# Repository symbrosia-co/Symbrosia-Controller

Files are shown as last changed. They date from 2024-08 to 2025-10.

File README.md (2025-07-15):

# The Symbrosia Controller
As originally designed, the Symbrosia Controller is a low cost, robust, controller designed for aquaculture.  Initially developed to support on-shore seaweed farming operations in Kailua Kona, Hawai'i, the Symbrosia Controller features a customized, low-cost sensor suite and integrated control functions tailored to meet the unique demands of these environments. 

In addition to commercial use, we envision the Symbrosia Controller as a powerful educational tool. By promoting literacy in electronics, programming, and agricultural management, we hope to empower individuals and communities to innovate and thrive in the agricultural sector. Our goal is to create a community where knowledge and technology are shared to drive sustainable agricultural practices and food security worldwide.

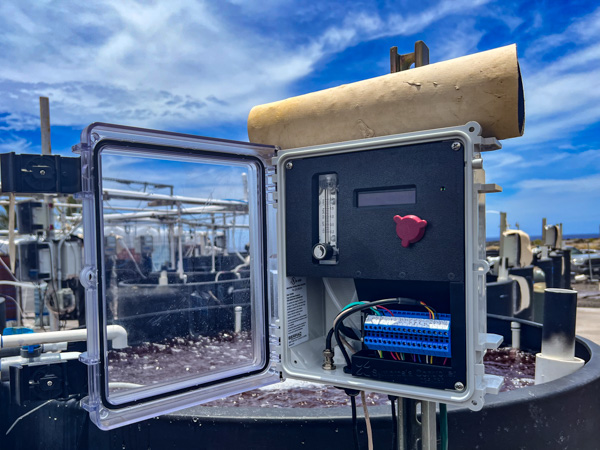
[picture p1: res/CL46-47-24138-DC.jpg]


## Background
The Symbrosia controller was developed for in-house use as a lower-cost alternative to the PLC-based and commercial off-the-shelf systems we use for algae tank and bioreactor control.  In addition to controlling the tanks there were a few other needs, places where a little remote control and monitoring is invaluable.  With the availability of WiFi processors like the ESP32 automating these functions was a practical option.

Thus the Symbrosia Controller was born…  An ESP32 wedded to a circuit board that contains the most commonly needed interfaces. A water quality sensor amplifier, some temperature inputs, a couple analog inputs, along with some relays and transistor outputs for controlling external devices like valves and pumps. 

While there are commercial solutions available, we have had mixed experience with them... The available commercial controllers are expensive and tend to provide “closed garden” systems where it becomes difficult to retrieve data outside of dedicated application software.  There is also limited or no support for integrating this equipment into a wider system.  While a number of small-scale, open source solutions do exist, none of the devices we have reviewed are fully developed into robust, industrial solutions.  As a result of our experience the Symbrosia controller offers a number of key advantages…

+ Designed from the ground up as a network appliance with full WiFi access.
+ A standard industrial ModbusTCP interface, a well established interface supported by a vast array of software and solutions available in the market.
+ A simple and effective user interface allowing access to key settings.
+ A well thought out and flexible control arrangement allowing automated control of pH, temperature, or other parameters.
+ A range of inputs that address the usual aquaculture needs...
  + One fully isolated water quality amplifier (for pH, ORP, etc.)
  + Two Pt100 temperature inputs
  + Two general purpose analog inputs that can be used with 0-5V, 0-10V, or 4-20mA signals, these can also be used as simple digital inputs.
  + Two relay outputs
  + Two open collector digital outputs
+ Good calibration solutions in place for the analog inputs
+ Semi-automated pH calibration built into the software for use with 7ph, and 4pH or 10pH reference solutions.
+ A complete solution ready for deployment in real applications.  Use it as designed and published, or change the hardware or code to suit your own needs.

Communication is via 2.4GHz WiFi, thus no cabling beyond power, or perhaps your sensors is required, a very real concern when salt water is involved and locations are scattered across a large facility. 2.4GHz offers much increased range for applications that do not require the bandwidth of higher frequencies.

For remote monitoring a ModbusTCP interface is implemented.  This allows easy integration with custom software or standard industrial SCADA systems.  While most programming languages like Python have ModbusTCP libraries available to allow connections with a few lines of code.

There are many options for designing and building a device like this.  The philosophy used in the design was carefully considered...

+ The controller is designed to be constructed and maintained by anyone with modest electronics knowledge and skills. Unless changing features is desired, no programming is required to set up and use the controller.
+ Complex solutions or specialized parts were avoided.  Rather parts that are commonly available, inexpensive, and likely to remain available for some time to come were chosen for the design.
+ An open source programming platform is used so that development tools are available at no cost, specifically the Arduino platform.
+ An open source schematic capture PCB CAD package was used, specifically KiCad. The CAD files may be used or edited at no cost beyond learning to use the software.

An example of the commonly available part philosophy can be found in the display.  There was great temptation to use a newer OLED color graphical display that would be both fun and attractive.  Rather a mundane 16x2 LCD character display was chosen.  The LDC display is very standard, inexpensive, robust in outdoor settings, available from multiple vendors, and is likely to remain available for a decade or two.  Still, a version based on an OLED display may exist someday just for the fun of it.

Another good example of this is in using a development module for the ESP32 rather than laying out the ESP32 and support electronics directly onto the main PCB.  While much of the design is surface mount, larger packages were used, this allows the entire PCB to be assembled by hand with no more specialized equipment than a decent soldering iron.

Likewise using the Arduino programming platform provides an approachable simplicity that is easily learned.  A huge array of support exists on the web with a robust development community.  Libraries to support Arduino are available from many sources that allow the use of a wide array of sensors, chips, or ready to use modules.

With the controller proving its usefulness across our algae production facility a further decision was made…  To release the controller to the community as an open source device.  Symbrosia is publishing the complete plans…  Schematic, BOM, PCB, 3D models, code, and user manual.

There is nothing exotic or particularly special here.  The Symbrosia Controller is the result of taking a number of parts and solutions that are available in the community and weaving them into a well thought out and robust solution.  The controller has been a good solution for us, maybe you can use it as well.

The Symbrosia Team

## Hardware
The Symbrosia Controler is a single circuit board that measures 120 x 92mm (4.71" x 3.62").  The board mounts an LCD display, a rotaty encoder for user input, and a pair of 8 circuit headers that permit easy connection of power and field wiring.  

The PCB assembly is designed to be mounted in either a simple case for DIN rail mounting, or for direct mounting in a control panel where the display and control knob are easily accessible.  Examples of both of these mountings can be found in the documention here including 3D models for the case.

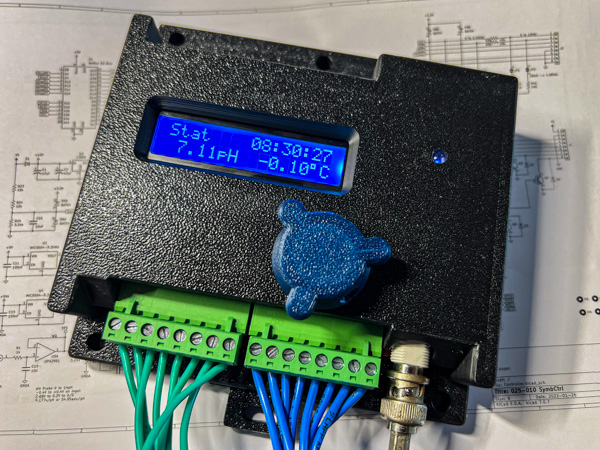
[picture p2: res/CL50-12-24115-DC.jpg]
A SymbCtrl in the DIN mount case


## Software
There are several software elements to the controller, all can be found in this repository.  While you may simply download everything here, an easier solution would be to install a copy of [GitHub desktop](https://desktop.github.com/download/).  Synchronizing with Github would allow you to keep an always up-to-date version available for use.

### Firmware
Firmware for the Symbrosia Controller was wriiten in the Arduino Framework for ESP-32.  The Arduino ecosystem is open source, free, and is amazing well supported by an enormous user community.  If you do not know how to use an Arduino device it is a good skill to learn, an incredibly useful tool to have in your skillset.

Compiling and downloading firmware to the controller is most easily accomplished by downloading the free [Arduino IDE](https://www.arduino.cc/en/software) and configuring it for use with the ESP32.  Additionally a few libraries will need to be loaded, this can be done with the library tool in the IDE.

### SyView
Setup and configuration is done through access to the Modbus regiaters.  Doing this by hand would be tedious.  To simplify this task SyView, a Python GUI is provided that gives easy access to all of the setup registers in an organized graphical app.  SyView also allows downloading complete configurations so they may be stored or loaded to multiple units with a single click. 

### MbMon
MbMon is a ModbusTCP data logger.  This script is often used to do simple datalogging for testing and short experiments.  An XML configuration file is used to designate a few Modbus devices on a local network.  The specified registers are monitored and if needed logged to a CSV file that can be used for data analysis.

MbMon will work with any ModbusTCP device including SymbCtrl, it can also serve as example code for writing your own logging application.

## Examples
Currently three sample systems are documented here, use these setups as is, or modify them to your own needs...

* [Tank or PBR controller](/samples/TankController/)
* [CO<sub>2</sub> Tapping Point Monitor](/samples/CO2Monitor/)
* [Weather Station](/samples/weather/)
  
Each of these designs are provided with schematics, 3D models, and setup files for the Symbrosia Controller.



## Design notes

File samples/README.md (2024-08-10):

# Samples
Several sample uses and configurations of the Symbrosia Controller are presented here..
[Tank or PBR controller with CO<sub>2</sub>](/TankController)
[CO<sub>2</sub> Tapping Point Monitor](/CO2Monitor)
[Weather Station](/weather)

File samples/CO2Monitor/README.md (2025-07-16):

# CO<sub>2</sub> Monitor

This example uses a simple pressure monitor to provide an alarm before a CO<sub>2</sub> cylinder is exhausted.

There is a complication in using a simple pressure sensor to monitor a CO<sub>2</sub> cylinder.  As CO<sub>2</sub> is stored as a liquid under pressure in the cylinder, the pressure in the tank is not determined by the amount of gas remaining, but rather by the boiling point of CO<sub>2</sub>.  Thus the amount of remaining gas cannot be measured by monitoring the pressure as it could be with air as done in scuba tanks.

The working pressure of the tank will remain at 50 to 70 Bar (700-1000 PSI), depending on ambient temperture, until the last liquid boils off.  Only once the liquid is gone will the pressure begin to drop as the last gas from the tank is used.  Setting an alarm threshhold of around 35 Bar (500 PSI) will allow a bit of warning before the available supply of gas is totally expended.

If proper determination of the amount of remaining CO<sub>2</sub> is desired the most practical method is to place the cylinder on a scale to directly measure the weight of the remaining gas.  As some scales do offer an analog output this output could be connected to a Symbrosia controller to provide remote monitoring and alarms.



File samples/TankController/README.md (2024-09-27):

# Tank or PBR Controller with CO<sub>2</sub>

A tank controller using SymbCtrlThe primary use of the Symbrosia Controller is as a culture tank or photo-bioreactor controller.  In such a role the controller can monitor and control water temperature, pH, and potentially other parameters as needed.

With up to five sensors the conditions of a culture vessel can be throughly monitored.  This includes one water quality sensor (pH, ORP, or similar), two temperature sensors, and two general purpose analog sensors.  Likewise four outputs allow control of the usual tank or PBR conditions such as CO<sub>2</sub> sparging and temperature control.

Documented here are the standard tank control boxes as used on the Symbrosia cultivation pads.  This is a control box built in a commonly available enclosure using standard parts.

A 3D printed frame is used to mount the various components into the enclosure in an organized and robust manner.  The use of standard DIN rail terminal blocks makes field wiring to sensors and valves easy to use and maintain.  CO<sub>2</sub> sparging is handled using a built in valve and flow gauge.

## Arrangement

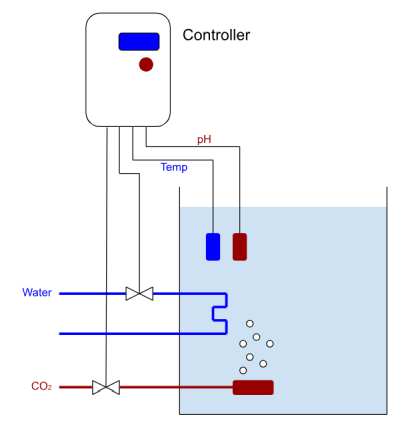
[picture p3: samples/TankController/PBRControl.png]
Tank or PBR Control
Any experienced aquaculture technician will find no surprises here, the controller is arranged exactly as one would expect.  In this case both temperature and pH control are implmented for use in algae culture.

Temperature control may be implemented with cool water circulating through a heat exchanger (as shown in the figure), direct addition of cool water, or conversely by use of a heater to warm rather than cool if the need demands.  In any case one of the controller relays can be used to actuate this control.  The onboard relays are rated at 240Vac and 5A, if a larger load such as a large heater or pump is required the onboard relay may be used to control a larger relay or contactor.

As shown, pH control is implemented in a very traditional manner, simply monitoring with a pH probe and when needed sparging CO<sub>2</sub> directly into the PBR or tank.

Built as documented below the controller should be capable of controlling tanks from a few tens of liters to a few thousand liters.  Larger tanks will require larger valves to allow more flow and well considered placement of sensors.  If two temperature sensors are needed in a large tank the Symbrosia Controller can be configured to min/max or average the two readings and use the result.

## Documentation

* [Schematic and parts](025-030SymbCtrlPBRController.pdf)
* [OpenSCAD source file]()
* [3D models ready for slicing](025-055SymbCtrlSubframeModel.zip)
  * [Upper Subframe](025-056SubframeUpper.stl)
  * [Lower Subframe](025-057SubframeLower.stl)
  * [DIN End Block](025-059TBlockEnd.stl)
  * [Control Knob](025-058ControlKnob.stl)
  * [Drill Guide](DrillGuide.stl)
* [Sample configuration file](StandardTank.xml)

The sample configuration file can be loaded into the controller using SyView.  This configuration assumes that the various accessories are connected to the controller as shown in the controller schematic above.

## Purchasing

All the needed parts can be purchased through the usual online vendors...

* Electronic components - Digikey (www.digikey.com) or Mouser (www.mouser.com)
* PCB - JLCPCB (www.jlcpcb.com) or Advanced PCB (www.advancedpcb.com)
* Valve - WIC Valve [2ACK-1/4-12VDC-G](https://wicvalve.com/product/1-4-inch-fast-response-air-water-electric-solenoid-valve-nc/)
* Flow Gauge - Omega [FL-2002](https://www.omega.com/en-us/flow-instruments/flow-meters/variable-area-flow-meters/fl2000-series/p/FL-2002) or Dwyer [VFA-23](https://dwyer-inst.com/en/products/flow/flowmeters/series-vf-visi-floatr-acrylic-flowmeter.html)
* Enclosure - Home Depot [Serpac I342HL](https://www.homedepot.com/p/Serpac-11-8-in-L-x-10-2-in-W-x-5-5-in-H-Cabinent-Enclosure-Polycarbonate-Clear-Hinged-Latch-Top-Gray-Bottom-I342HL-TCBG/303702896)

Note that the flow meter model needed may require checking against the size of tank or PBR and the CO<sub>2</sub> flow rates needed to control pH.

## 3D Printing

Many standard 3D printers can print the parts needed for the design shown here with a couple considerations...

* While PLA is the most popular filament to print, it is easy, very forgiving, and cheap, the problem is that PLA can soften and distort in a hot environment.  Some early prototypes of the Symbrosia Controller suffered this fate when the enclosures sat in Hawaiian sunlight.  All parts should be printed in ABS, PETG, ASA, or some other heat tolerant filament.  These materials take a bit more work and understanding to print.
* The largest part is 207mm x 143mm, some of the smaller printers cannot accomodate a part this large.   Check your printer build plate size, many of the most popular modern printers will have no issues (Ender 3, Bambu X1, Prusa i3 MK3, etc.).

## Construction

## Use Considerations

This controller has been in use for some years now, with a large number constructed and in use in multiple aquaculture facilites.  While it has served well, a few things have been noted...

* In order to prevent corrosion and damage to the electronics the enclosure is normally sealed, all wiring made through cable glands that prevent any water ingress.  There is a price to this, the enclosure interior can get quite hot when in full sunlight.  Some provision must be made to shade the unit, either mounting in a shaded location or providing a simple cover that can be used to keep sunlight off the case, particularly keeping sunlight from shining into the clear cover. This can be seen in the photo above.
*  It is desirable to mount the controller above water level.  This addresses two issues, it prevents water from coming in the CO<sub>2</sub> tubing through the sparger thus preventing damage to the CO<sub>2</sub> supply valve.  We have also found the tanks and PBR's full of seawater make excellent WiFi signal blockers.  Keeping the controllers above tank level provides clear line-of-sight to the WiFi access points mounted on poles around our cultivation area.
*  Seawater and electrical power are a dangerous combination.  Around the Symbrosia cultivation area 120V power is carefully handled.  All receptacles are installed 3ft or higher off the ground to reduce the chance of spray or splashing, all outlets are covered by in-use receptacles.  While the controllers take 120V in, no output connection (sensors, valves, etc.) uses greater than 12Vdc.  Thus the majority of wiring around the tanks and PBR's is kept at a safe voltage.  We typically install a larger 12Vdc @ 6A (72W) power supply in the control boxes to provide ample power for valves and other accessories.

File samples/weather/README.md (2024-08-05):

# SymbCtrl Weather Station

The weather station is configured to support the sesnors that provide the most useful values to an outdoor aquaculture.

While a dedicated weather station may be desired, there is an option...  In a modest to large outdoor installation is likely that there are unused input channels on the various controllers scattered across a cultivation yard.  Adding weather instruments to these otherwise unused channels would allow excellent weather monitoring without a dedicated weather station.  The method of connection would be the same as detailed here.

* An air temperature sensor
* PAR sensor
* Rain gauge

## Sensors

### Air Temperature Sensor
A Pt100 temperature sensor is used for ambient temperature, simply connected to one of the temperature inputs on the controller.  To ensure accurate readings the sensor needs to be located in free air away from other objects, ideally at a height above the ground.  

The temperature sensor also needs to be shaded from sunlight. this is done with a small louvered enclosure.  A 3D model for a small solar radiation enclosure is provided here in the repository.  This should be printed using a sunlight resistant plastic such as ABS or ASA.   

### PAR Sensor
A commercial PAR (Photosynthetically Active Radiation) sensor is connected to one of the general purpose analog inputs.  This provides a calibrated measurement of the avalable solar radiation avalable for algae growth.

A good example of such a sesnor would be the [Apogee SQ-515-SS or SQ-514-SS sensors](https://www.apogeeinstruments.com/full-spectrum-quantum-par-meters-and-sensors).  These provide a 0 to 5V or 4-20mA signal that can be directly connected to the analog inputs on a Symbrosia Controller.

### Rain Gauge
A standard tipping bucket rain gauge is connected to one of the digital inputs.

Using the software counter provides a direct measurement of rainfall on your facility.  Configuring the counter with a daily reset then gives a daily precipitation count that can be easily logged.

## Hardware

### SymbCtrl PCB

### Housing

### 3D Prints

### Wiring

## Software

### Firmware
The standard SymbCtrl firmware should be loaded

## SyWx
A simple weather station GUI is provided that displays and logs the weather station data.  This is a Python and TCl GUI that should run on any operating system.

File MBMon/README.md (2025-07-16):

# MbMon
MbMon is a simple Modbus logging utility, it can monitor any ModbusTCP device and store data into a CSV file.  The application is a Python GUI that may be used as is, or examined as an example of how to write you own Modbus scripts.

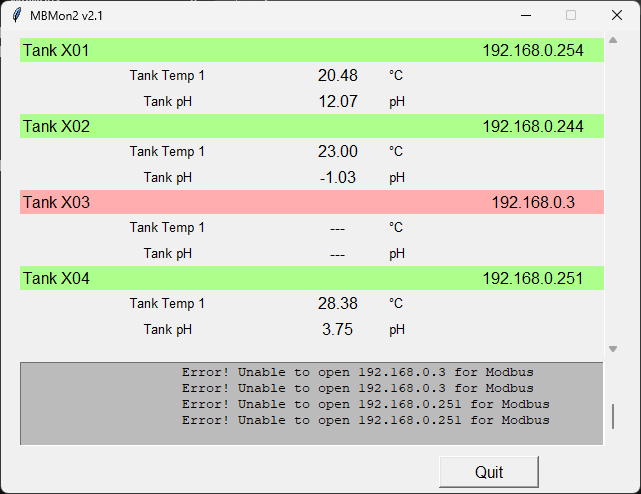
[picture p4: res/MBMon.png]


The program reads a configuration file and simply runs, reading from the specified Modbus devices and registers and logging the data to the specified CSV file.

Each device is shown in a section with the device name and IP address displayed.  Beneath a header each datum is displayed in table format.  The background color to the header indicates connection status to the device, green or red.  Occasional red may be displayed if network connectivity is poor or temporarily interrupted, the data request will be re-attempted.  A prolonged connection error will result in the data values being dashed out indicating stale and invalid data.

Below the data table is a log window that records a record of logging events and communications errors.

## Installation
MBMon is installed by simply copying the MBMon directory to your desired location on a local hard drive.

There are three subdirectories in the folder for MBMon...
+ **lib** should contain the required file MBScan.py
+ **setup** will likewise hold the configuration file MBMon.xml (see below)
+ **log** which will hold the resulting CSV files.  If **log** does not exist the directory will be created when MBMon is run the first time.

## Dependencies
MBMon requires Python 3.x be installed on the local computer.  Along with Python there is one additional library, pyModbusTCP required.  The latest version of Python should be downloaded and installed from the Python.org website.  The library for pyModbusTCP may be installed directly using PIP (recommended) or from the Github archive.

+ [Python.org](https://www.python.org/) Follow the install links of the main page for your operating system

To install pyModbusTCP using PIP use the following at a command line...

+ Unix/Linix systems  **sudo pip3 install pyModbusTCP**
+ Windows **pip install pyModbusTCP**

pyModbusTCP support...

+ [pyModbusTCP at Github](https://github.com/sourceperl/pyModbusTCP)
+ [pyModbusTCP documentation at Read the Docs](https://pymodbustcp.readthedocs.io/en/stable/index.html)

## Configuration file
MbMon is configured using an XML file that stores the IP address and register addresses of the desired data.  This file should be named MBMon.xml and be placed the the **setup** subdirectory.  A couple example configuration files are provided in the Github repository.

```xml
<!-- Modbus Monitor Configuration File -->
<configuration>
  <scanInterval>1</scanInterval>
  <logInterval>120</logInterval>
  <logName>TankCtrl</logName>
  <device>
    <name>Tank X01</name>
    <ipAddr>192.168.0.111</ipAddr>
    <port>502</port>
    <datum>
      <name>Tank Temp</name>
      <addr>22</addr>
      <type>float</type>
      <unit>°C</unit>
      <dispPrec>2</dispPrec>
      <logPrec>2</logPrec>
      <log>True</log>
    </datum>
    <datum>
      <name>Tank pH</name>
      <addr>20</addr>
      <type>float</type>
      <unit>pH</unit>
      <dispPrec>1</dispPrec>
      <logPrec>2</logPrec>
      <log>True</log>
    </datum>
    <datum>
      <name>CO2 Valve</name>
      <addr>12</addr>
      <type>coil</type>
      <log>True</log>
    </datum>
  </device>
</configuration>
```

A description of each XML field is below.

+ **configuration:** This tag encompasses the entire MBMon configuration file
+ **scanInterval:** Specified the rate at which the device should be queried for data over the network in seconds.  Can be set to longer intervals for equipment that cannot support high data rates.
+ **logInterval:** Specifies the interval for writing to the log file in seconds.
+ **logname:** Base filename for the resulting data file, the name will have the date and the filename extension **.xml** appended to the supplied name.  Files will be created when needed, if the file already exists data will be appended each logging interval.
+ **name:** A short descriptive name for the device, this will be used to organize the data for display during logging and will be appended to the column header in the CSV file.
+ **ipAddr:** The local IP address for the ModbusTCP device.
+ **port:** The port for ModbusTCP access, usually the default ModbusTCP port 502.
+ **datum:** Used to specify a specific item of data.
+ **name:** A descriptive name for the item of data, this will be used to format the data for display when logging and as the column header in the CSV file.
+ **addr:** The ModbusTCP register address, addressing starting at zero is used. It is important to specify a type to read the cirrect address in the device, coil registers are used for coil or boolean values, else holding registers are read.
+ **type:** The type of data expected, the following values are permissable, the allowable types are as follows...
  + coil: A boolean value (true or false) from a Modbus coil register
  + bool: Same as coil
  + hold: An unsigned 16bit integer value from a holding register
  + uint: Same as hold
  + int: A signed 16 bit integer value from a holding register
  + long: an unsigned long integer of 32 bits from two consecutive holding registers, the address should point at the first register
  + float: a 32 bit IEEE-754 floating point number from two consecutive holding registers, the address should point at the first register
+ **unit:** The units (if any), this is used for data display during logging, this field is not required and is not used for coil or boolean types
+ **dispPrec:** The number of decimal points to be displayed during logging, this field is not required or used for non-floating point values
+ **logPrec:** The number of decimal points to be recorded in the log file, this field is not required or used for non-floating point values
+ **log:** If **true** the value is logged to the CSV file, if **false** the value is displayed only.



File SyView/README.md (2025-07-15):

# SyView
SyView is the Python configuration utility for the Symbrosia Controller. With SyView a user can configure and test a controller, as well as save and load configurations to and from the controller.

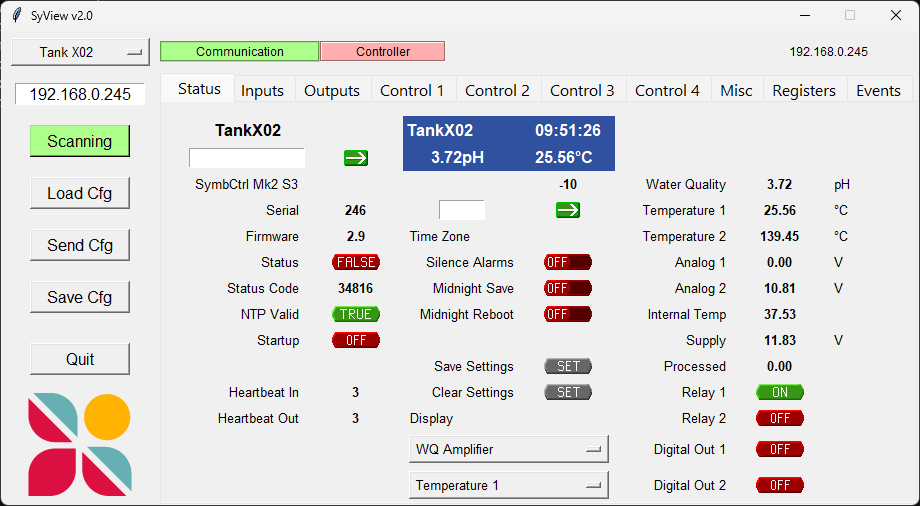
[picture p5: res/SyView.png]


SyView is a Python 3.x application that should run on any modern operating system.

## Installation
SyView is installed by simply copying the SyView directory to your desired location on a local hard drive.

There are three subdirectories in the folder for SyView...
+ **lib** should contain the various required files for SyView
+ **configuration** will likewise hold the configuration file configuration.xml (see below)

## Dependencies
SyView requires Python 3.x be installed on the local computer.  Along with Python there is one additional library, pyModbusTCP required.  The latest version of Python should be downloaded and installed from the Python.org website.  The library for pyModbusTCP may be installed directly using PIP (recommended) or from the Github archive.

+ [Python.org](https://www.python.org/) Follow the install links of the main page for your operating system

To install pyModbusTCP using PIP use the following at a command line...

+ Unix/Linix systems  **sudo pip3 install pyModbusTCP**
+ Windows **pip install pyModbusTCP**

pyModbusTCP support...

+ [pyModbusTCP at Github](https://github.com/sourceperl/pyModbusTCP)
+ [pyModbusTCP documentation at Read the Docs](https://pymodbustcp.readthedocs.io/en/stable/index.html)

## Configuration file
SyView is configured using an XML file that stores the IP address and register addresses of the desired data.  This file should be named configuration.xml and be placed the the **cfg** subdirectory.  An example configuration file is provided in the Github repository.

```xml
<!-- SyView Configuration File -->

<configuration>
  <ctrl name='Tank X01'>
    <model>SyCtrl Mk2</model>
    <description>Tank Controller</description>
    <address>192.168.0.24</address>
  </ctrl>
  <ctrl name='Tank X02'>
    <model>SyCtrl Mk2</model>
    <description>Tank Controller</description>
    <address>192.168.0.245</address>
  </ctrl>
</configuration>
```

A description of each XML field is below.

+ **configuration** This tag encompasses the entire configuration file
+ **model** The specific controller model, currently only Mark 2's are supported
+ **description** A quick description identifying the controller
+ **address** The IP address of the target Symbrosia controller



---

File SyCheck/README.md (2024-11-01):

# SyCheck
SyCheck performs configuration checks on any number of deployed controllers.

Assuring that each controller in an installation is configured correctly can be a time consuming task.  SyCheck will retrieve the configuration for each controller on the network and compare the configuration against a reference file, producing a report of any differences found.

A set of configuration files are required.  The first file is an XML file contianing the IP addresses of any deployed controllers and the name of the reference file that controller should be configured with.  Also required are one or more reference files to compare against the controllers in the installation.

SyCheck is a Python 3.x application that should run on any operating system.

One library is required beyond the standard Python install, the [pyModbusTCP library by Loic Lefebvre](https://pypi.org/project/pyModbusTCP/).  This can be installed by through pip...

* sudo pip install pyModbusTCP (for Linix/Unix)
* pip install pyModbusTCP (for Windows)

## Configuration file
The configuration file is an XML file that contains a record for each controller on the network you wish to check.

```xml
<?xml version="1.0" encoding="UTF-8"?>
<!--
  SyCheck Configuration File
  - Installation specific information
-->
<configuration>
  <ctrl name='Tank 1'>
    <address>192.168.1.20</address>
    <ref>TankSetup.xml</ref>
  </ctrl>
  <ctrl name='Tank 2'>
    <address>192.168.1.21</address>
    <ref>TankSetup.xml</ref>
  </ctrl>
</configuration>
```

You may have multiple reference files so that each controller may use one of several different configurations

## Reference File
The reference file uses the same file format used by SyView to upload and download controller configurations.  Simply using SyView to save the setup of a known good controller can be used as a starting point.

Some editing of this file is suggested.  Only the fields present in the file will be checked, fields not requiring checks can be deleted.  Fields such as unit name will always fail (unless you name all of your controllers the same, probably not good practice;)

```xml
<?xml version="1.0" encoding="UTF-8"?>
<!--
  Tank configuration file
  2024Jun22 08:45:25
-->
<configuration>
  <register name="WQName">pH</register>
  <register name="Temp1Name">Tank Temp</register>
  <register name="Temp2Name"></register>
  <register name="Input1Name"></register>
  <register name="Input2Name"></register>
  <register name="Relay1Name">Cooling Valve</register>
  <register name="Relay2Name"></register>
  <register name="Output1Name">CO2 Valve</register>
  <register name="Output2Name"></register>
  <register name="Control1Name">pH</register>
  <register name="Control2Name">Cooling</register>
  <register name="Control3Name">Lights</register>
  <register name="Control4Name"></register>
  <register name="StatusDisp1">1</register>
  <register name="StatusDisp2">2</register>
  <register name="TimeZone">-10</register>
  <register name="WQSensorUnits">3</register>
  <register name="Temp1Units">1</register>
  <register name="Temp2Units">1</register>
  <register name="Analog1Units">5</register>
  <register name="Analog2Units">5</register>
  <register name="IntTempUnits">1</register>
  <register name="SupVoltUnits">5</register>
  <register name="WQOffset">-0.20</register>
  <register name="Temp1Offset">0.10</register>
  <register name="Temp2Offset">0.00</register>
  <register name="Analog1Offset">0.00</register>
  <register name="Analog2Offset">0.00</register>
  <register name="WQGain">1.08</register>
  <register name="Temp1Gain">1.00</register>
  <register name="Temp2Gain">1.00</register>
  <register name="Analog1Gain">1.00</register>
  <register name="Analog2Gain">1.00</register>
  <register name="Ctrl1Input">1</register>
  <register name="Ctrl1Output">13</register>
  <register name="Ctrl1Setpoint">7.50</register>
  <register name="Ctrl1Hysteresis">0.20</register>
  <register name="Ctrl1AlarmPtLow">7.00</register>
  <register name="Ctrl1AlarmPtHigh">8.00</register>
  <register name="Ctrl1OffTime">0</register>
  <register name="Ctrl1OnTime">0</register>
  <register name="Ctrl2Input">2</register>
  <register name="Ctrl2Output">11</register>
  <register name="Ctrl2Setpoint">23.50</register>
  <register name="Ctrl2Hysteresis">1.00</register>
  <register name="Ctrl2AlarmPtLow">20.00</register>
  <register name="Ctrl2AlarmPtHigh">28.00</register>
  <register name="Ctrl2OffTime">0</register>
  <register name="Ctrl2OnTime">0</register>
  <register name="Ctrl3Input">0</register>
  <register name="Ctrl3Output">0</register>
  <register name="Ctrl3Setpoint">6.00</register>
  <register name="Ctrl3Hysteresis">12.00</register>
  <register name="Ctrl3AlarmPtLow">0.00</register>
  <register name="Ctrl3AlarmPtHigh">30.00</register>
  <register name="Ctrl3OffTime">0</register>
  <register name="Ctrl3OnTime">0</register>
  <register name="Ctrl4Input">0</register>
  <register name="Ctrl4Output">0</register>
  <register name="Ctrl4Setpoint">1.50</register>
  <register name="Ctrl4Hysteresis">0.50</register>
  <register name="Ctrl4AlarmPtLow">0.00</register>
  <register name="Ctrl4AlarmPtHigh">2.00</register>
  <register name="Ctrl4OffTime">0</register>
  <register name="Ctrl4OnTime">0</register>
  <register name="LogicInA">0</register>
  <register name="LogicInB">0</register>
  <register name="LogicFunction">0</register>
  <register name="ToDStartHour">6</register>
  <register name="ToDStartMin">0</register>
  <register name="ToDStopHour">18</register>
  <register name="ToDStopMin">0</register>
  <register name="ToDOutput1">13</register>
  <register name="ToDOutput2">0</register>
  <register name="ToDOutput3">0</register>
  <register name="ToDOutput4">0</register>
  <register name="CountSource">13</register>
  <register name="CountRstIntv">2</register>
  <register name="TimerSource">13</register>
  <register name="TimerRstIntv">2</register>
  <register name="LogInterval">10</register>
  <register name="LogNumber">0</register>
  <register name="LogItem">0</register>
  <register name="LogData">0.00</register>
  <register name="ProcessChanA">0</register>
  <register name="ProcessChanB">0</register>
  <register name="ProcessID">0</register>
  <register name="MidnightSave">False</register>
  <register name="MidnightReset">False</register>
  <register name="SilenceAlarms">False</register>
  <register name="Relay1Request">False</register>
  <register name="Relay2Request">False</register>
  <register name="Dout1Request">False</register>
  <register name="Dout2Request">False</register>
  <register name="VState1">False</register>
  <register name="VState2">False</register>
  <register name="Ctrl1Enable">True</register>
  <register name="Ctrl2Enable">True</register>
  <register name="Ctrl3Enable">False</register>
  <register name="Ctrl4Enable">False</register>
  <register name="Ctrl1High">True</register>
  <register name="Ctrl2High">True</register>
  <register name="Ctrl3High">False</register>
  <register name="Ctrl4High">False</register>
  <register name="CounterEnable">False</register>
  <register name="TimerEnable">False</register>
  <register name="ToDEnable">True</register>
</configuration>
```

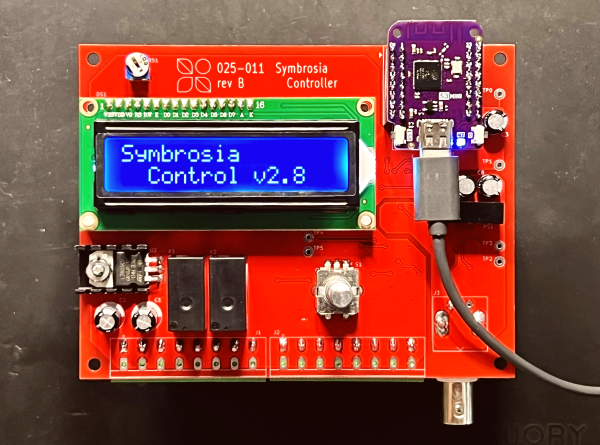
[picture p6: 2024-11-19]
res/SymbCtrlPCB.png

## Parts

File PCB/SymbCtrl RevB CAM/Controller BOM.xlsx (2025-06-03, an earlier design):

Comment | Designator | Footprint | JLCPCB
Ceramic capacitor, 100nF 50V 1206 | C4, C5, C6, C10, C11, C12, C13, C14, C15, C16, C17, C18, C22, C24, C25, C26 | 1206 | C24497
Ceramic capacitor, 10nF 50V 1206 | C21, C29, C30, C31 | 1206 | C521245
Ceramic capacitor, 1nF 50V 1206 | C20, C27, C28 | 1206 | C107207
Rectifier diode, 100V 1A SMA | D1, D2, D3, D4, D5 | SMA | C156295
Schottky diode 30V 100mA dual series SOT23 | D6, D7, D8, D9, D10, D11, D12, D13 | SOT-23 | C47546
NPN Transistor 40V 1A SOT89 | Q1, Q2, Q3, Q4 | SOT-89-3 | C460011
1.00kΩ 1% resistor, 1/4W 1206 | R1, R6, R27, R28, R31, R32, R33, R34 | 1206 | C131398
3.24kΩ 1% resistor, 1/4W 1206 | R2, R7, R8, R9, R10, R11, R12, R13, R14, R25 | 1206 | C488775
10.0kΩ 1% resistor, 1/4W 1206 | R3, R5, R17, R18, R19, R20, R23, R24, R29, R35, R36, R45, R46, R47, R48, R49, R50 | 1206 | C132649
1.20kΩ 1% resistor, 1/4W 1206 | R4 | 1206 | C185265
82.5Ω 1% resistor, 1/4W 1206 | R15, R16 | 1206 | C229817
332kΩ 1% resistor, 1/4W 1206 | R21, R22 | 1206 | C137311
331Ω 1% resistor, 1/4W 1206 | R26 | 1206 | C114944
10kΩ thermistor 1206 B25/85 3630K | R30 | 1208 | C525390
3.01kΩ 1% resistor, 1/4W 1206 | R39, R40 | 1206 | C229594
249Ω 1% resistor, 1/2W 1210 | R43, R44 | 1210 | C723700
MIC5504 3.3V regulator, SOT23 | U3, U4 | SOT-23-5 | C88419
Dual op-amp, low Ib, SOIC-8 | U5, U8 | SOIC-8 | C2878324
MCP3021 10bit AtoD, SOT23-5 | U6 | SOT-23-5 | C128576
ISO1640BDR isolated I2C | U7 | SOIC-8 | C5122339
TL431 programmable voltage reference, SOIC-8 | U9 | SOIC-8 | C6970
MCP3208 12 bit 8 channel AtoD | U10 | SOIC-16 | C16939

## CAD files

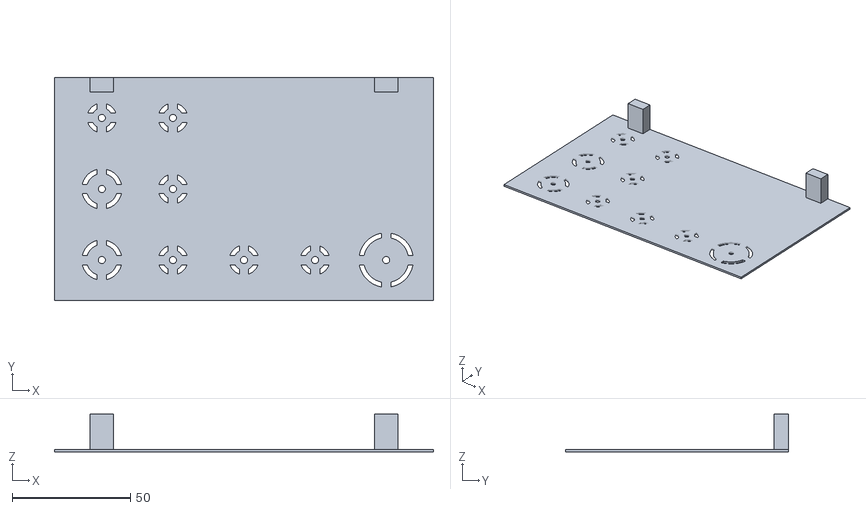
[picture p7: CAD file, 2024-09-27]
samples/TankController/DrillGuide.stl
160.0 x 94.0 x 16.0

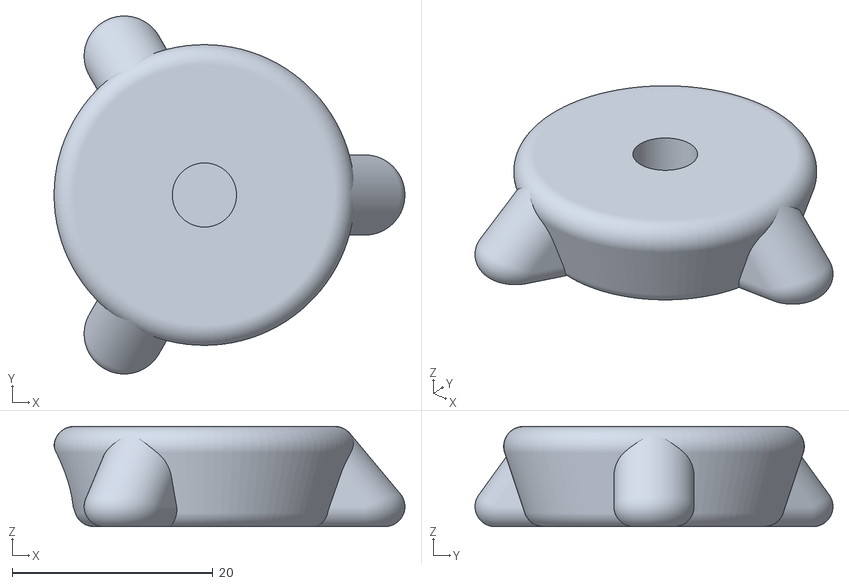
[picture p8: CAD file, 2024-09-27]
samples/TankController/025-058ControlKnob.stl
35.0 x 35.7 x 10.0

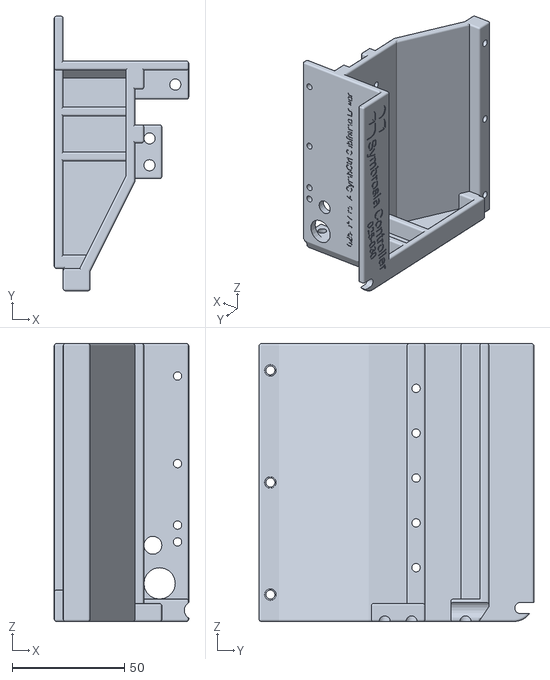
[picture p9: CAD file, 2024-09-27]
samples/TankController/025-057SubframeLower.stl
60.0 x 122.5 x 124.0

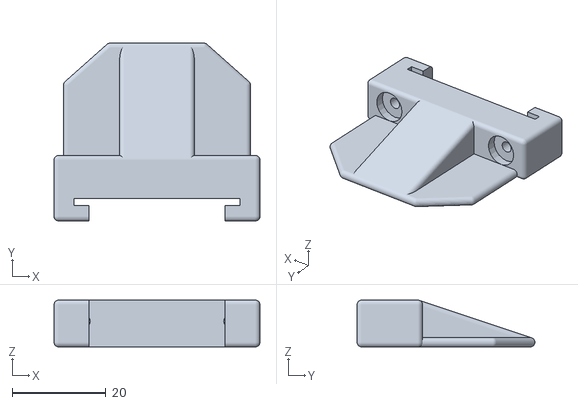
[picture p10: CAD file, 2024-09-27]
samples/TankController/025-059TBlockEnd.stl
44.0 x 38.0 x 10.00

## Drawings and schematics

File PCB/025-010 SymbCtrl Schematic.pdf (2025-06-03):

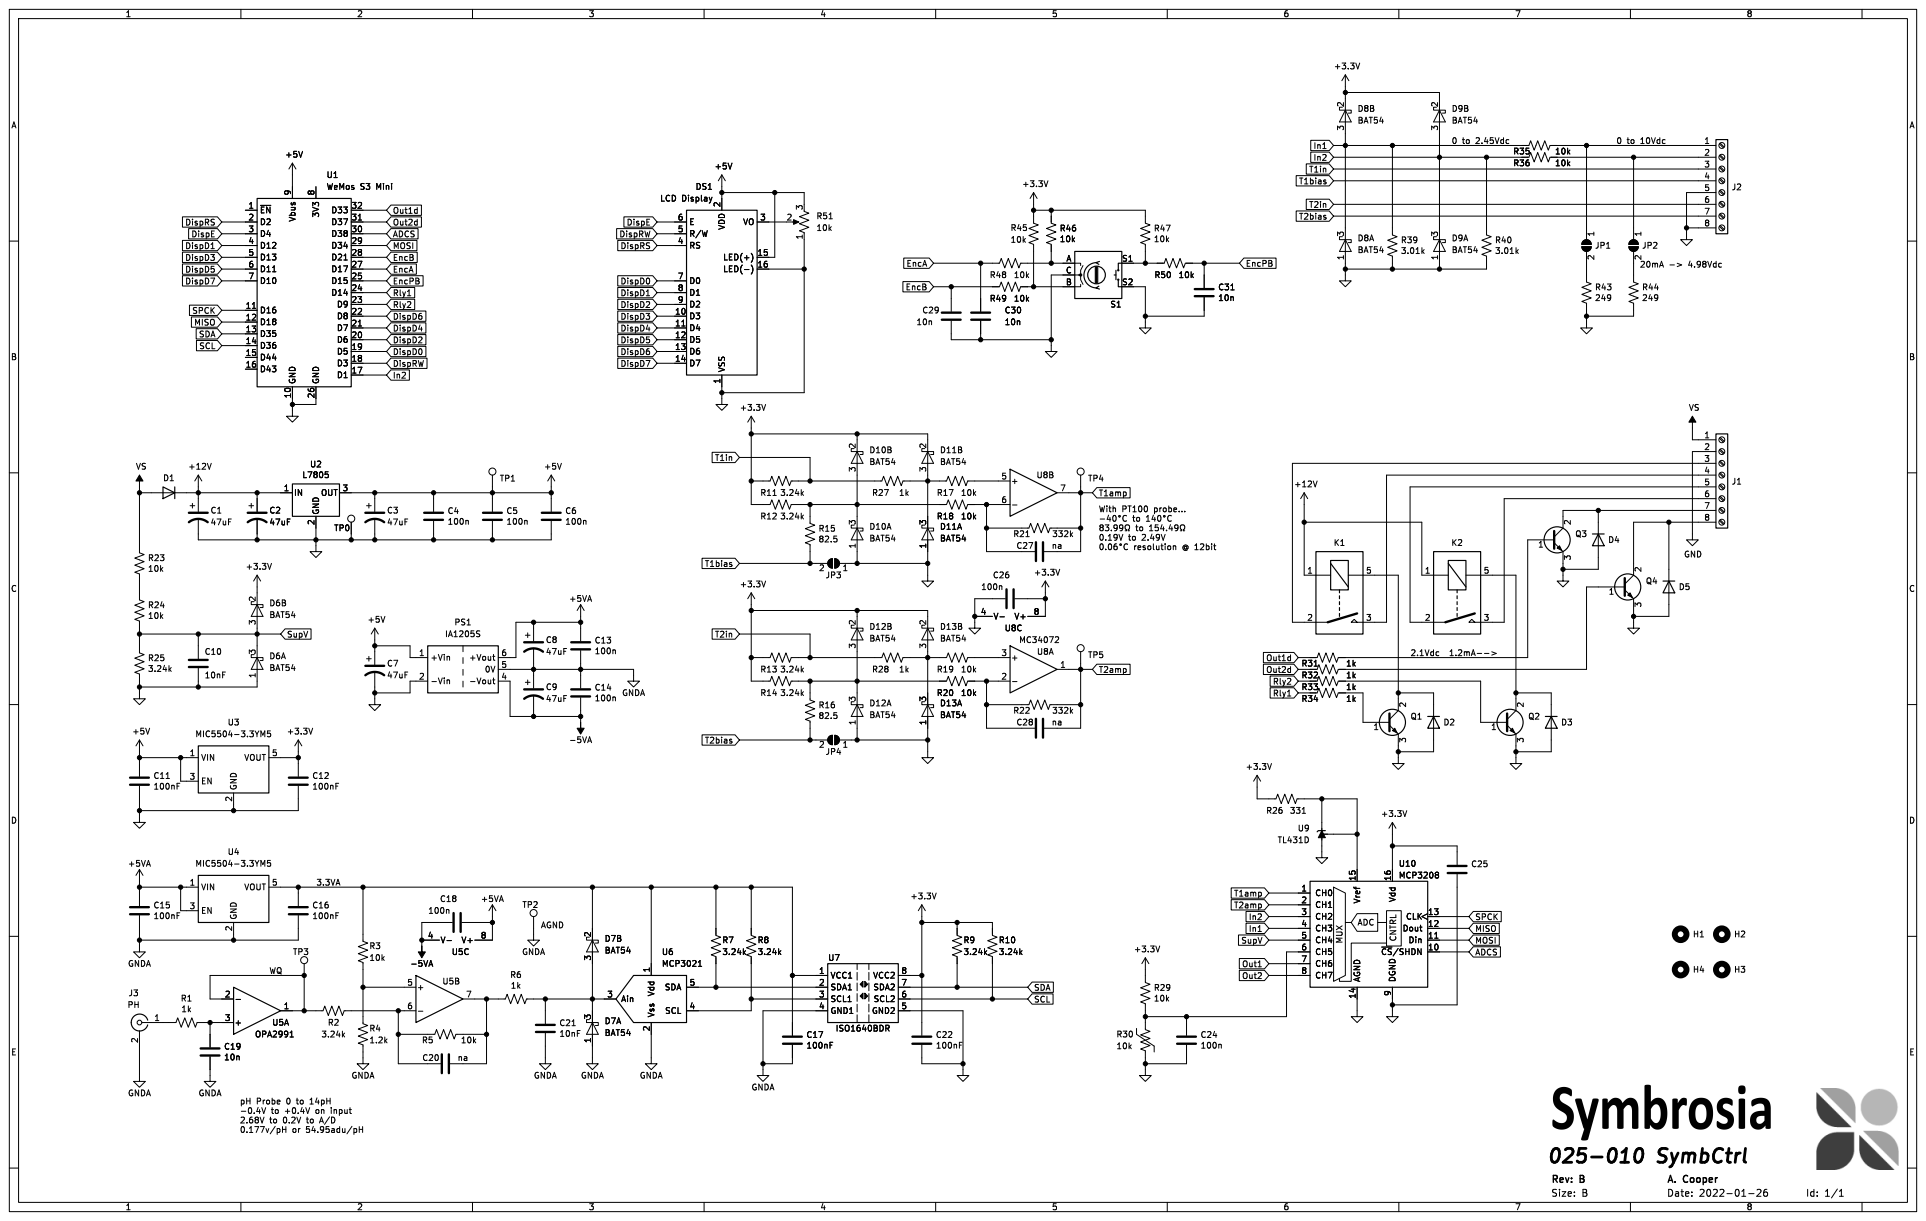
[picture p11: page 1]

2 OUT 3 TP0 R34 1k U10 MCP3208 CH0 1 ~{CS}/SHDN10 Din 11 Dout 12 CLK 13 AGND 14 Vref 15 Vdd 16 CH1 2 CH2 3 CH3 4 CH4 5 CH5 6 CH6 7 CH7 8 DGND

1 Vss 2 Ain 3 SCL 4 SDA 5 U6 MCP3021 R20 10k 1 3D13A

1 Vss 2 Ain 3 SCL 4 SDA 5 R7

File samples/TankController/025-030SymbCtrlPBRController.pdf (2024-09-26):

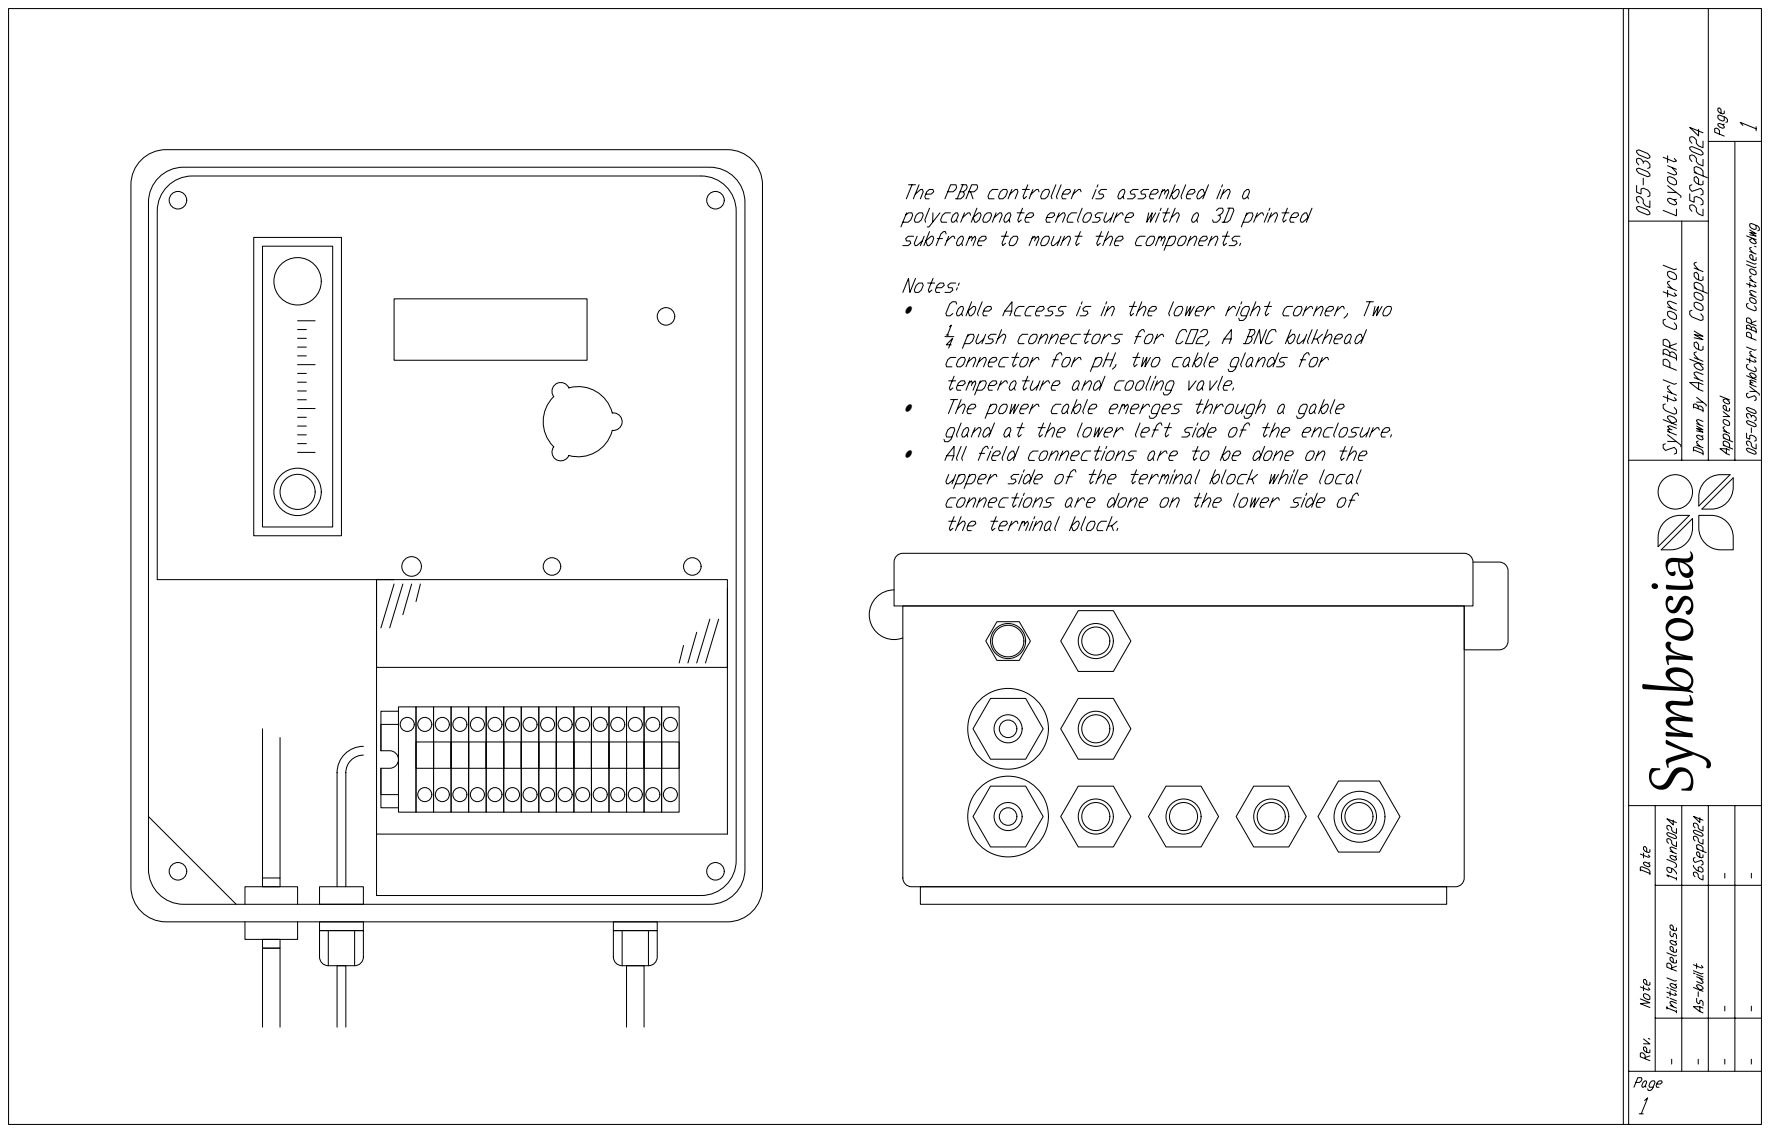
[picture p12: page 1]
Symbrosia

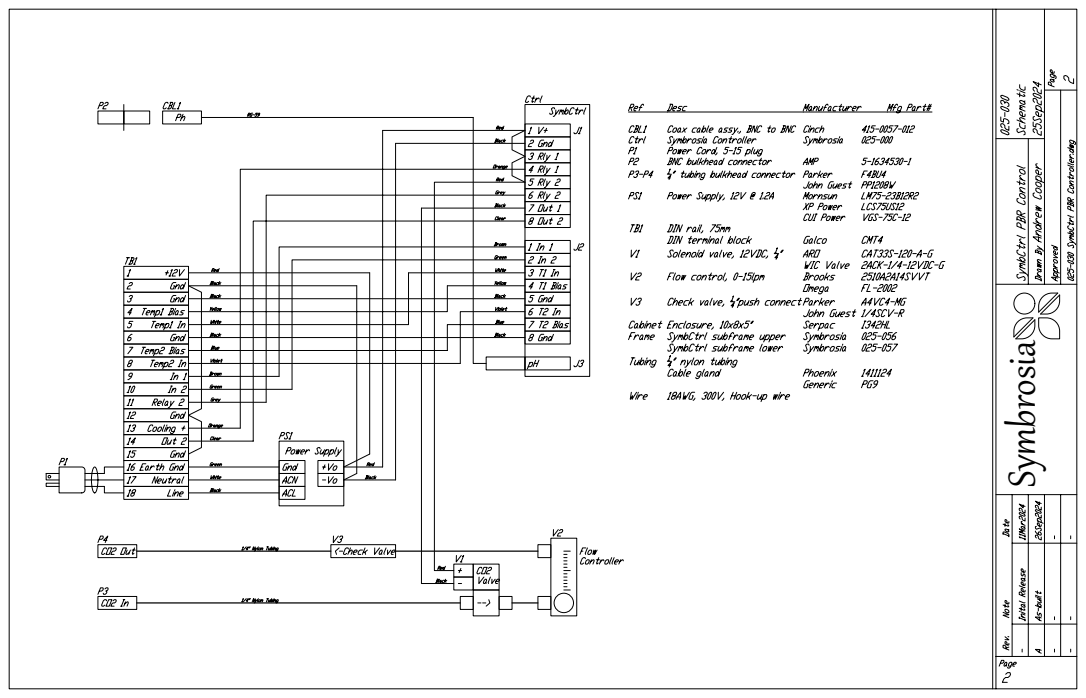
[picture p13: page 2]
Symbrosia

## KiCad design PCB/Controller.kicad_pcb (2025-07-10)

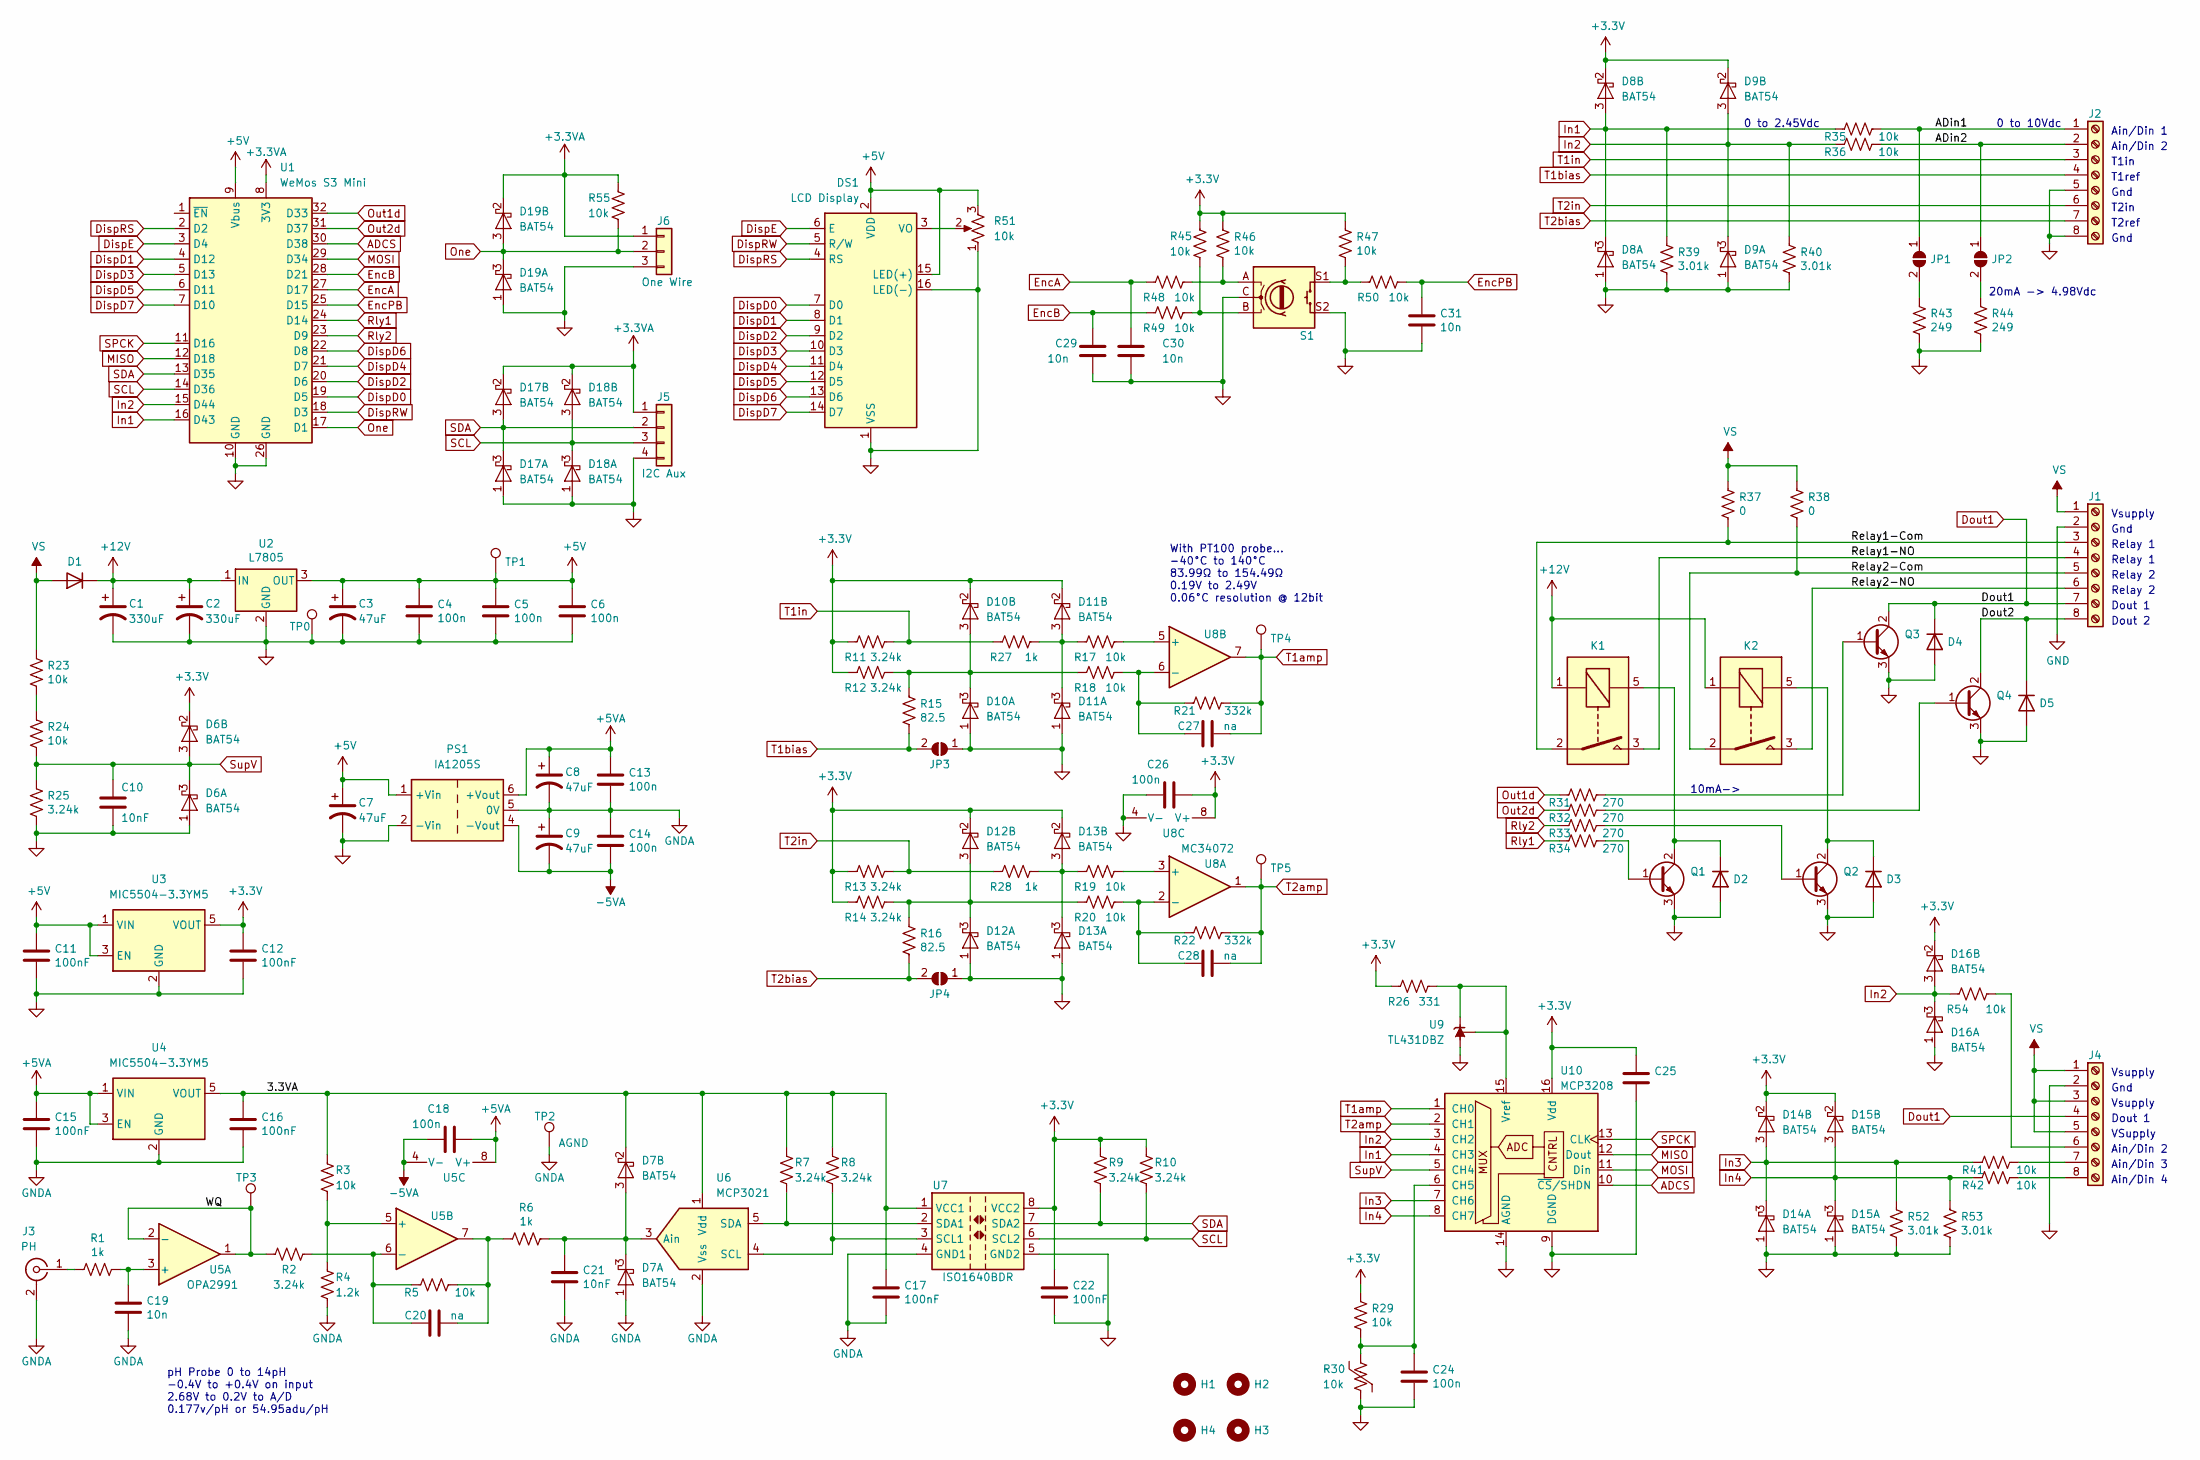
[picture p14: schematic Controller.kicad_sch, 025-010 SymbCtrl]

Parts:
C1, C2: 330uF; CP_Radial_D10.0mm_P5.00mm
C3, C7, C8, C9: 47uF; CP_Radial_D6.3mm_P2.50mm
C4, C5, C6, C13, C14, C18, C24, C25, C26: 100n; C_1206_3216Metric_Pad1.33x1.80mm_HandSolder
C10, C21: 10nF; C_1206_3216Metric_Pad1.33x1.80mm_HandSolder
C11, C12, C15, C16, C17, C22: 100nF; C_1206_3216Metric_Pad1.33x1.80mm_HandSolder
C19, C29, C30, C31: 10n; C_1206_3216Metric_Pad1.33x1.80mm_HandSolder
C20, C27, C28: na; C_1206_3216Metric_Pad1.33x1.80mm_HandSolder
D1, D2, D3, D4, D5: US1A; D_SMA
D6, D7, D8, D9, D10, D11, D12, D13, D14, D15, D16, D17, D18, D19: BAT54; SOT-23
DS1: LCD Display; WC1602A
H1, H2, H3, H4: MountingHole; MountingHole_3.5mm
J1, J2: Screw_Terminal_01x08; PhoenixContact_MSTBA_2,5_8-G-5,08_1x08_P5.08mm_Horizontal
J3: PH; BNC_Amphenol_B6252HB_Reversible
J4: Screw_Terminal_01x08; PhoenixContact_MSTBVA_2,5_8-G-5,08_1x08_P5.08mm_Vertical
J5: I2C Aux; Molex_KK-254_AE-6410-04A_1x04_P2.54mm_Vertical
J6: One Wire; Molex_KK-254_AE-6410-03A_1x03_P2.54mm_Vertical
JP1: In1 4-20; SolderJumper-2_P1.3mm_Open_RoundedPad1.0x1.5mm
JP2: In2 4-20; SolderJumper-2_P1.3mm_Open_RoundedPad1.0x1.5mm
JP3: T1 2/3Wire; SolderJumper-2_P1.3mm_Open_RoundedPad1.0x1.5mm
JP4: T2 2/3Wire; SolderJumper-2_P1.3mm_Open_RoundedPad1.0x1.5mm
K1, K2: TE_PCH-1xxx2M; Relay_SPST_TE_PCH-1xxx2M
PS1: IA1205S; Converter_DCDC_XP_POWER-IAxxxxS_THT
Q1, Q2, Q3, Q4: BCX56; SOT-89-3_Handsoldering
R1, R6, R27, R28: 1k; R_1206_3216Metric_Pad1.30x1.75mm_HandSolder
R2, R7, R8, R9, R10, R11, R12, R13, R14, R25: 3.24k; R_1206_3216Metric_Pad1.30x1.75mm_HandSolder
R3, R5, R17, R18, R19, R20, R23, R24, R29, R35, R36, R41, R42, R45, R46, R47, R48, R49, R50, R54, R55: 10k; R_1206_3216Metric_Pad1.30x1.75mm_HandSolder
R4: 1.2k; R_1206_3216Metric_Pad1.30x1.75mm_HandSolder
R15, R16: 82.5; R_1206_3216Metric_Pad1.30x1.75mm_HandSolder
R21, R22: 332k; R_1206_3216Metric_Pad1.30x1.75mm_HandSolder
R26: 331; R_1206_3216Metric_Pad1.30x1.75mm_HandSolder
R30: 10k; R_0805_2012Metric_Pad1.20x1.40mm_HandSolder
R31, R32, R33, R34: 270; R_1206_3216Metric_Pad1.30x1.75mm_HandSolder
R37, R38: 0; R_1206_3216Metric_Pad1.30x1.75mm_HandSolder
R39, R40, R52, R53: 3.01k; R_1206_3216Metric_Pad1.30x1.75mm_HandSolder
R43, R44: 249; R_1210_3225Metric_Pad1.30x2.65mm_HandSolder
R51: 10k; Potentiometer_Piher_PT-6-V_Vertical_Hole
S1: RotaryEncoder_Switch; RotaryEncoder_Alps_EC11E-Switch_Vertical_H20mm_CircularMoun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
TP0: Gnd; TestPoint_THTPad_D2.5mm_Drill1.2mm
TP1: +5V; TestPoint_THTPad_D2.5mm_Drill1.2mm
TP2: AGND; TestPoint_THTPad_D2.5mm_Drill1.2mm
TP3: WQ; TestPoint_THTPad_D2.5mm_Drill1.2mm
TP4: Temp2; TestPoint_THTPad_D2.5mm_Drill1.2mm
TP5: Temp1; TestPoint_THTPad_D2.5mm_Drill1.2mm
U1: WeMos S3 Mini; WEMOS S2 Mini
U2: L7805; TO-220-3_Horizontal_TabDown
U3, U4: MIC5504-3.3YM5; SOT-23-5_HandSoldering
U5: OPA2991; SOIC-8_3.9x4.9mm_P1.27mm
U6: MCP3021; SOT-23-5_HandSoldering
U7: ISO1640BDR; SO-8_3.9x4.9mm_P1.27mm
U8: MC34072; SOIC-8_3.9x4.9mm_P1.27mm
U9: TL431DBZ; SOT-23
U10: MCP3208; SOIC-16_3.9x9.9mm_P1.27mm

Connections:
+3.3V: C12.1, C22.1, C25.1, C26.1, D6.2 (K), D8.2 (K), D9.2 (K), D10.2 (K), D11.2 (K), D12.2 (K), D13.2 (K), D14.2 (K), D15.2 (K), D16.2 (K), R9.1, R10.1, R11.1, R12.1, R13.1, R14.1, R26.1, R29.2, R45.2, R46.2, R47.2, U3.5 (VOUT), U7.8 (VCC2), U8.8 (V+), U10.16 (Vdd)
+3.3VA: D17.2 (K), D18.2 (K), D19.2 (K), J5.1, J6.1, R55.2, U1.8 (3V3)
+5V: C3.1, C4.1, C5.1, C6.1, C7.1, C11.1, DS1.2 (VDD), DS1.15 (LED(+)), PS1.1 (+Vin), R51.3, TP1.1, U1.9 (Vbus), U2.3 (OUT), U3.1 (VIN), U3.3 (EN)
+5VA: C8.1, C13.1, C15.1, C18.1, PS1.6 (+Vout), U4.1 (VIN), U4.3 (EN), U5.8 (V+)
+12V: C1.1, C2.1, D1.1 (K), K1.1, K2.1, U2.1 (IN)
-5VA: C9.2, C14.2, C18.2, PS1.4 (-Vout), U5.4 (V-)
/3.3VA: C16.1, C17.1, D7.2 (K), R3.1, R7.1, R8.1, U4.5 (VOUT), U6.1 (Vdd), U7.1 (VCC1)
/ADin1: J2.1, JP1.1 (A), R35.2
/ADin2: J2.2, JP2.1 (A), R36.2
/Dout2: D5.1 (K), J1.8, Q4.2 (C)
/Relay1-Com: J1.3, K1.2, R37.1
/Relay1-NO: J1.4, K1.3
/Relay2-Com: J1.5, K2.2, R38.1
/Relay2-NO: J1.6, K2.3
/WQ: R2.2, TP3.1, U5.1, U5.2 (-)
ADCS: U1.30 (D38), U10.10 (~CS/SHDN)
DispD0: DS1.7 (D0), U1.19 (D5)
DispD1: DS1.8 (D1), U1.4 (D12)
DispD2: DS1.9 (D2), U1.20 (D6)
DispD3: DS1.10 (D3), U1.5 (D13)
DispD4: DS1.11 (D4), U1.21 (D7)
DispD5: DS1.12 (D5), U1.6 (D11)
DispD6: DS1.13 (D6), U1.22 (D8)
DispD7: DS1.14 (D7), U1.7 (D10)
DispE: DS1.6 (E), U1.3 (D4)
DispRS: DS1.4 (RS), U1.2 (D2)
DispRW: DS1.5 (R/W), U1.18 (D3)
Dout1: D4.1 (K), J1.7, J4.4, Q3.2 (C)
EncA: C30.1, R48.1, U1.27 (D17)
EncB: C29.1, R49.1, U1.28 (D21)
EncPB: C31.1, R50.2, U1.25 (D15)
GND: C1.2, C2.2, C3.2, C4.2, C5.2, C6.2, C7.2, C10.2, C11.2, C12.2, C22.2, C24.2, C25.2, C26.2, C29.2, C30.2, C31.2, D2.2 (A), D3.2 (A), D4.2 (A), D5.2 (A), D6.1 (A), D8.1 (A), D9.1 (A), D10.1 (A), D11.1 (A), D12.1 (A), D13.1 (A), D14.1 (A), D15.1 (A), D16.1 (A), D17.1 (A), D18.1 (A), D19.1 (A), DS1.1 (VSS), DS1.16 (LED(-)), J1.2, J2.5, J2.8, J4.2, J5.4, J6.3, JP3.1 (A), JP4.1 (A), PS1.2 (-Vin), Q1.3 (E), Q2.3 (E), Q3.3 (E), Q4.3 (E), R25.1, R30.2, R39.1, R40.1, R43.1, R44.1, R51.1, R52.1, R53.1, S1.C, S1.S2, TP0.1, U1.10 (GND), U1.26 (GND), U2.2 (GND), U3.2 (GND), U7.5 (GND2), U8.4 (V-), U9.3 (A), U10.9 (DGND), U10.14 (AGND)
GNDA: C8.2, C9.1, C13.2, C14.1, C15.2, C16.2, C17.2, C19.2, C21.2, D7.1 (A), J3.2 (Ext), PS1.5 (0V), R4.2, TP2.1, U4.2 (GND), U6.2 (Vss), U7.4 (GND1)
In1: D8.3 (COM), R35.1, R39.2, U1.16 (D43), U10.4 (CH3)
In2: D9.3 (COM), D16.3 (COM), R36.1, R40.2, R54.1, U1.15 (D44), U10.3 (CH2)
In3: D14.3 (COM), R41.1, R52.2, U10.7 (CH6)
In4: D15.3 (COM), R42.1, R53.2, U10.8 (CH7)
MISO: U1.12 (D18), U10.12 (Dout)
MOSI: U1.29 (D34), U10.11 (Din)
unnamed: C20.1, R5.2, R6.2, U5.7
unnamed: D2.1 (K), K1.5, Q1.2 (C)
unnamed: D3.1 (K), K2.5, Q2.2 (C)
unnamed: C21.1, D7.3 (COM), R6.1, U6.3 (Ain)
unnamed: D10.3 (COM), R12.2, R15.2, R18.1
unnamed: D11.3 (COM), R17.1, R27.2
unnamed: D12.3 (COM), R14.2, R16.2, R20.1
unnamed: D13.3 (COM), R19.1, R28.2
unnamed: DS1.3 (VO), R51.2
unnamed: J3.1 (In), R1.2
unnamed: J4.6, R54.2
unnamed: J4.7, R41.2
unnamed: J4.8, R42.2
unnamed: JP1.2 (B), R43.2
unnamed: JP2.2 (B), R44.2
unnamed: Q1.1 (B), R34.2
unnamed: Q2.1 (B), R33.2
unnamed: Q3.1 (B), R31.2
unnamed: Q4.1 (B), R32.2
unnamed: R23.1, R24.2
unnamed: R45.1, R49.2, S1.B
unnamed: R46.1, R48.2, S1.A
unnamed: R47.1, R50.1, S1.S1
unnamed: C19.1, R1.1, U5.3 (+)
unnamed: R3.2, R4.1, U5.5 (+)
unnamed: C20.2, R2.1, R5.1, U5.6 (-)
unnamed: R8.2, U6.4 (SCL), U7.3 (SCL1)
unnamed: R7.2, U6.5 (SDA), U7.2 (SDA1)
unnamed: R19.2, U8.3 (+)
unnamed: C28.2, R20.2, R22.1, U8.2 (-)
unnamed: R17.2, U8.5 (+)
unnamed: C27.2, R18.2, R21.1, U8.6 (-)
unnamed: C24.1, R29.1, R30.1, U10.6 (CH5)
unnamed: R26.2, U9.1 (K), U9.2 (REF), U10.15 (Vref)
One: D19.3 (COM), J6.2, R55.1, U1.17 (D1)
Out1d: R31.1, U1.32 (D33)
Out2d: R32.1, U1.31 (D37)
Rly1: R34.1, U1.24 (D14)
Rly2: R33.1, U1.23 (D9)
SCL: D18.3 (COM), J5.3, R10.2, U1.14 (D36), U7.6 (SCL2)
SDA: D17.3 (COM), J5.2, R9.2, U1.13 (D35), U7.7 (SDA2)
SPCK: U1.11 (D16), U10.13 (CLK)
SupV: C10.1, D6.3 (COM), R24.1, R25.2, U10.5 (CH4)
T1amp: C27.1, R21.2, TP4.1, U8.7, U10.1 (CH0)
T1bias: J2.4, JP3.2 (B), R15.1
T1in: J2.3, R11.2, R27.1
T2amp: C28.1, R22.2, TP5.1, U8.1, U10.2 (CH1)
T2bias: J2.7, JP4.2 (B), R16.1
T2in: J2.6, R13.2, R28.1
VS: D1.2 (A), J1.1, J4.1, J4.3, J4.5, R23.2, R37.2, R38.2

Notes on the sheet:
Gnd
Ain/Din 4
Dout 1
0 to 2.45Vdc
Relay 2
T2in
Vsupply
T2ref
20mA -> 4.98Vdc
Ain/Din 1
T1in
Relay 1
Ain/Din 2
pH Probe 0 to 14pH -0.4V to +0.4V on input 2.68V to 0.2V to A/D 0.177v/pH or 54.95adu/pH
VSupply
Ain/Din 3
10mA->
0 to 10Vdc
Dout 2
With PT100 probe... -40°C to 140°C 83.99Ω to 154.49Ω 0.19V to 2.49V 0.06°C resolution @ 12bit
T1ref

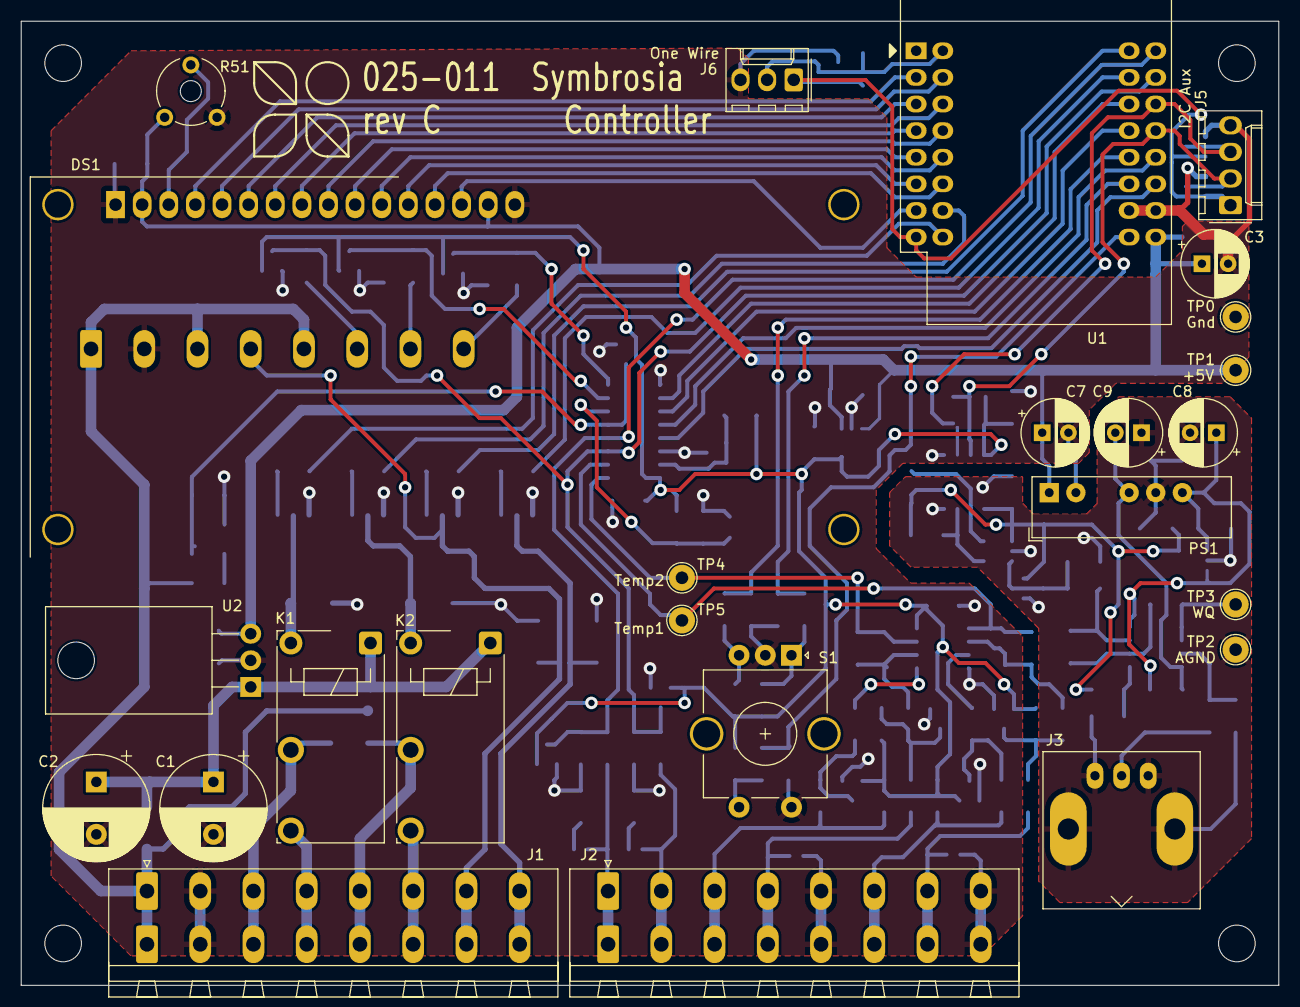
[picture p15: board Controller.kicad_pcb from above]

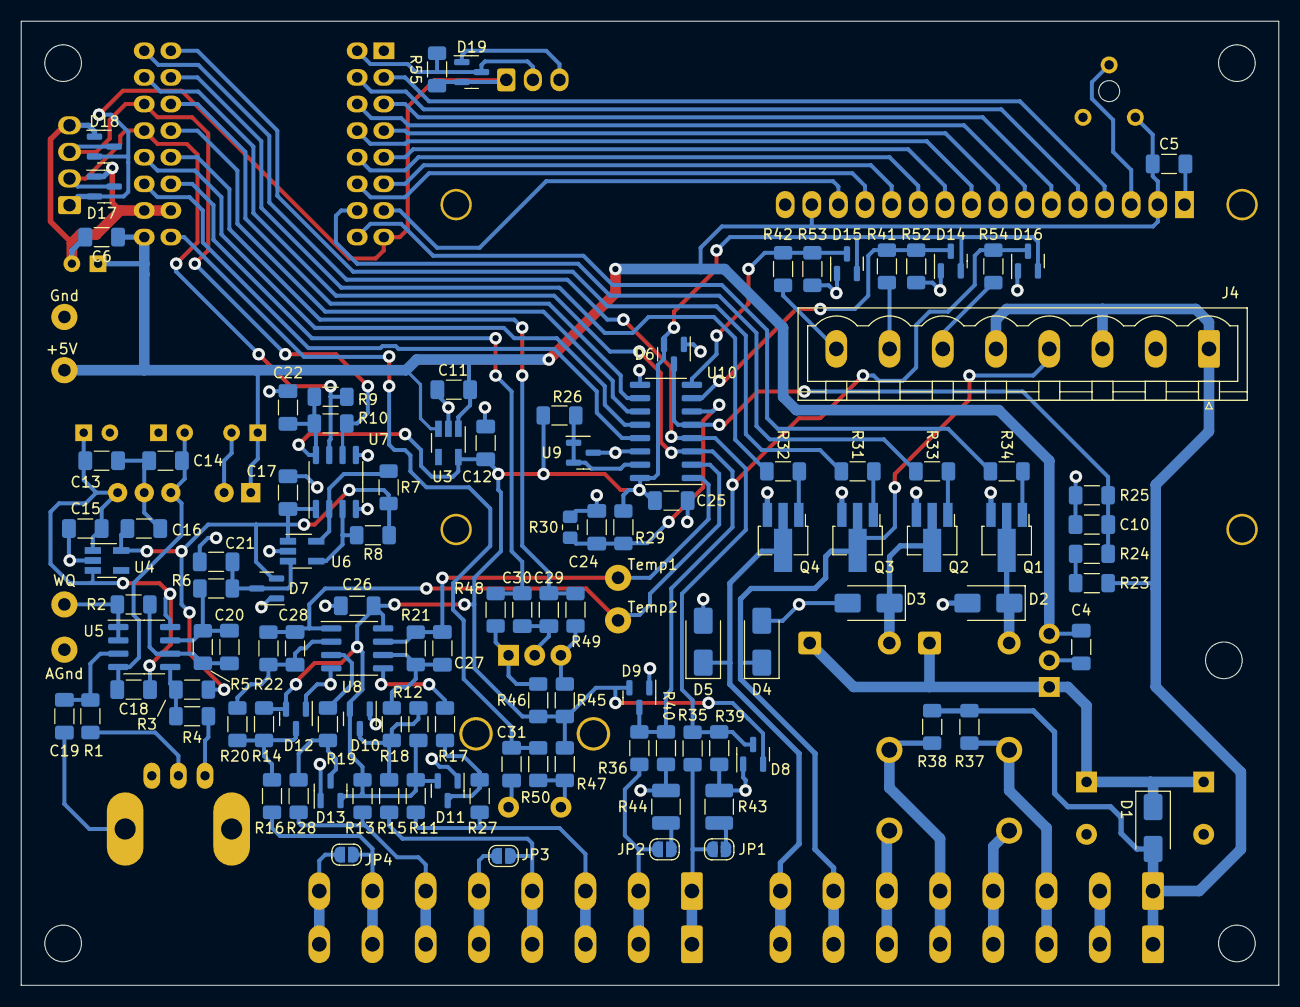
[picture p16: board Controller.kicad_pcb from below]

Board: 2 copper layers, 120.0 x 92.0 mm, 143 parts (114 on the bottom side), 89 nets.

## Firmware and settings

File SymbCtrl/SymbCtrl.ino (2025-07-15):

/*------------------------------------------------------------------------------

  SymbCtrl - The Symbrosia Aquaculture Controller
  Copyright © 2021 Symbrosia Inc.

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
-- required libraries ---------------------------------------------------------

  Library list...   (the following are required for the project)
  - Arduino
  - WiFi, v1.2.7
  - Wire, v2.0.0
  - SPI, v2.0.0
  - EEPROM, v2.0.0
  - LiquidCrystal, v1.0.7
  - ESP32Time, ESP32 RTC time support by Felix Biego v2.0.6
  - ModbusTCP, Modbus TCP support by Alexander Emelianov v4.1.0
  - ESP Rotary, rotary encoder support by Lennart Hennigs v2.1.1
  - Button2, pushbutton support by Lennart Hennigs v2.3.3
  - Adafruit Neopixel, support for the ESP32 RGB neopixel LED v1.12.3
  - MCP_ADC, handling for the MCP3208 AtoD by Rob Tillaart v0.5.1
  - MCP3X21, handling for the MCP3021 AtoD by Pavel Slama v1.0.1
  - esp32FOTA, support for over-the-air firmware update by Chris Joyce v0.2.9
  - ArduinoJSON, JSON file used in firmware update by Benoit Blanchon v7.2.1 

-- revision record ------------------------------------------------------------

  24Dec2021 v0.1 A. Cooper
  - initial version, based on Genesis controller
  17Jan2022 A. Cooper
  - converted dedicated control loops to three generic control loops
  - added 30 second startup delay
  10Feb2022 A. Cooper v0.9
  - revised to match new PCB layout
  - removed relay 3
  - added additional control loop, now four outputs and four control loops
  - added supply voltage monitor
  - added processed output
  - reconciled memory maps in memory.h, modbusCtrl.cpp, and documentation
  15Apr2022 A. Cooper
  - all PCB hardware tested and operational, hardware design frozen
  - most basic features now implemented and tested
  - logging will be postponed for first release
  - implemented midnight reset and autosave of parameters
  - added a number of front panel controls to enable/disable/reset
  - added pH calibration from front panel
  - revised memory maps for final release and cleanup from development
  - added status display with Saola RGB neopixel
  - added a clear settings bit to restore defaults in EEPROM
  - fixed memory.setStr bug  
  16Apr2022 A. Cooper
  - added the logic gate controller to handle digitial control
  - added a 1Hz flash register for the logic controller  
  - logic gate function added for multiple inputs including alarms
  - flasher added at 1Hz
  - added two virtual IO registers for the logic gate function
  - added status detection for alarms, low voltage, high temp
  17Apr2022 A. Cooper v1.0
  - first release candidate, deployed on two units
  23Apr2022 A. Cooper v1.1
  - allowed decimal time as control input value to enable time based control
  - added global silence for alarms
  - added unit data screen
  - modified status screen to allow selection of displayed values
  12May2022 A. Cooper v1.2
  - use controller name as WiFi host name, else SymbCtrl if no name set
  - fixed type bug in time based control, fractional hours and minutes not working
  - fixed output change bug, output stayed active when loop output changed
  - added temperature compensation to pH readings
  - display pH temp comp source on WQ screen
  - improved network recovery on outage
  - better handling of invalid NTP time, ToD and time based control inactive
  7July2022 A. Cooper v1.3
  - fixed calibration bug in WQ sensor
  - added dummy read to switch channels and stabilize readings
  - added WiFi network selection and SSID entry to WiFi screen
  - added second WiFi screen to user interface with nework info
  - added unit reset to unit info screen
  - increased analog averaging table to 40 samples
  31July2023 A. Cooper v1.4
  - added asterisk to the allowable WiFi password characters
  - added daily reset to counter and timer
  16Dec2023 v2.0 A. Cooper
  - modify for Mark 2 PCB's
  - use ESP32-S3 in the Wemos S3 Mini form factor
  - LCD interface to 8 bit bus
  - pH is handled by a galvanically isolated MCP3021 single input 10-bit
  AtoD converter using an I2C interface
  - all other AtoD uses 8 channels with an MCP3208 12-bit SAR
  AtoD with an SPI interface
  - rescale all conversion constants for new hardware
  18Jan2024 v2.1 A. Cooper
  - increased A/D averaging substantially
  20Mar2024 v2.1 A. Cooper
  - fixed temperature 2 units bug, using temperature 1 units to flag conversion
  20Mar2024 v2.4 A. Cooper
  - Added and tested support for Wemos ESP32-S2 Mini
  - removed support for ESP32 Saola and older rev PCB's, Rev A and later are supported
  - added limiting to some values upon modbus holding register write
  - finished timer and counter resets hourly and daily
  - better handling of WiFi connection, retries and detection of bad connection, loss of NTP time
  - added screen for internal temp and supply voltage
  - added combined alarm states for each control loop and overall
  - major update/rewrite to timeCtrl toproperly use ESP32 RTC in place of generic Arduino timekeeping library
  - added frequency counter to counter function
  - fixed temperature 2 units bug, using temperature 1 units to flag conversion
  - breaking changes to MCP_ADC library incorporated, now using 0.5.0
  - added offsetHdwr to compensate for average hardware temperature offset
  - added local control loop setpoint adjust
  - added local temperature calibration
  23Apr2024 v2.5 A. Cooper
  - changed temp out-of-range to -30 to 140 (before cal offsets)
  - fixed left scroll out of ScrWiFiDone bug
  - fixed incorrect pin on Digital Output 1 33 to 40 for ESP-S2 mini
  - expanded the alarm bits to add control alarms
  17Jul2024 v2.6 A. Cooper
  - Added alarm bits to the status register
  - revised ToD logic to change behavior, ToD active will reflect ToD enable
  - cleaned up code in TofDay
  - major modifications to control:service
    - added control enable with external sources
    - added one-shot enable
    - added minimim on/off time
  - removed a decimal point from status screen analog values
  - allow any IO channel on status display
  - changed from boxcar average to a tracking average in analogCtrl
  - added TofD to IO channel list
  - corrected bug: alarm if internal temp was in Deg F
  - major re-write of the processed reading, all methods now operate
  like priority in passing a value through
  - added CtoF to analogCtrl
  - some corrections to pH temperature calibration, tested successfully
  - apply gain and offset to analog inputs last using selected units
  - removed MCP3021 library, use direct calls to Wire
  - added auto I2C address search for MCP3021
  - a successful functional test performed
  - concat SymbCtrl to unit name to make network name
  08Oct2024 v2.7 A. Cooper
  - major re-write of userCtrl to clean up the methods for handling user
    input such as calibration and WiFi credential input, it needed it
  - solved WiFi.scanNetworks bug, would not initiate a scan when the
    previous network connection or connection attempt was not fully
    terminated, use WiFi.disconnect with a wifioff=true to fully
    disconnect and shutdown the conection before an SSID scan
  - change memory.save to memory.saveFloat in calibration routines
  - change memory.save to memory.saveWiFi in credential entry routine
  - restart userSetTime timeout on all encoder or button input
  - add manual offset adjustment to analog inputs
  - add indication of manual NTP fetch
  - re-write pH calibration process to reduce putton pushing
  - add simple offset adjustment to WQ input when not used for pH
  - change ToD logic to not use direct mode as long as any controller
    has the channel whether the controller is enabled or disabled
  - changed serial messages during EEPROM load
  - show sensor name on WQ screen
  - do not use priority for sum or difference in processed reading, lose
    any reading => invalid
  02Nov2024 v2.8 A. Cooper
  - Set up code for fota using esp32FOTA by Chris Joyce
  - new serial number assignment method at first boot on new unit
  - reserve bytes at start of flash for fixed information including
    serial number and hardware information
  - add setSerial, setHardware, and setProcessor methods to memory
  - add getSerial, getHardware, and getProcessor methods to memory
  - add getWQInstalled and setWQInstalled methods to memory
  - modify setup to handle fixed memory entry if needed on startup,
    setup will block while looping userCtrl.service, encoder, and button
  - in userCtrl add screens for fixed data entry
  - in userCtrl add screen for firmware update
  - in userCtrl move reset function to status screen
  - in userCtrl add firmware update to unit info screen
  11Apr2025 v2.9 A. Cooper
  - remove unused timer and counter enable
  - added time limited command, a command input that will only be valid for the
    duration specified, code in tlCtrl.cpp
  - added registers for time limited command, datTLCDuration 148,
    datTLCOutput 149, statTimeLimCmd 70, and statTimeLimFlag 71
  - expanded Modbus coil space to 80 registers
  - add code for manual output testing to userCtrl.cpp/drawOutputs
  - added use of TWDT to prevent overall lockups
  
  Known bugs...
  - none

------------------------------------------------------------------------------*/

//- Library includes -----------------------------------------------------------
#include <Arduino.h>
#include <WiFi.h>
#include <ModbusTCP.h>
#include <Wire.h>
#include <SPI.h>
#include <ESPRotary.h>
#include <Button2.h>
#include <esp32-hal-log.h>
#include <Adafruit_NeoPixel.h>
#include <esp_task_wdt.h>

//- Local includes -------------------------------------------------------------
#include "globals.h"
#include "memory.h"
#include "control.h"
#include "analogCtrl.h"
#include "procCtrl.h"
#include "modbusCtrl.h"
#include "timeCtrl.h"
#include "userCtrl.h"
#include "logicCtrl.h"
#include "todCtrl.h"
#include "tlCtrl.h"
#include "countCtrl.h"
#include "fotaCtrl.h"

//- Instantiate Local Libraries ------------------------------------------------
Memory     memory;
TimeCtrl   timeCtrl;
UserCtrl   userCtrl;
AnalogCtrl analogCtrl;
ProcCtrl   procCtrl;
Control    control;
LogicCtrl  logic;
ToDCtrl    todCtrl;
TLCtrl     tlCtrl;
CountCtrl  countCtrl;
FOtACtrl   fotaCtrl;

//- Instantiate IO Libraries ---------------------------------------------------
ESPRotary  encodeRot;
Button2    encodeButton;
#ifdef hardwareS3Mini  // only the S3 has an RGB LED
Adafruit_NeoPixel pixel(1, hdwrRGBLED, NEO_GRB + NEO_KHZ800);
#endif

//- Global variables -----------------------------------------------------------
boolean wifiStat= false;
IPAddress     wifiIPAddr;
unsigned long wifiTime= 0;
const bool    wifiOn= true;
unsigned long pixelTime= 0;

//- output control -------------------------------------------------------------
bool ctrlMatrix[ctrlOuts][ctrlSrcs];

//- watchdog configuration ----------------------------------------------------
// esp_task_wdt_config_t twdt_config = {
//         .timeout_ms= watchdogTime*1000,
//         .idle_core_mask= (1<<watchdogCores)-1, // Bitmask of all cores
//         .trigger_panic= true,
//     };
  
//- low level hardware --------------------------------------------------------- 
void setOutputs(){
  // move manual requests to control matrix
  for (int i=0;i<ctrlOuts;i++)
    ctrlMatrix[i][ctrlExtReq]= memory.getBool(statRelay1Request+i);
  if (!memory.getBool(statStartup))
    // set outputs based on control matrix
    // the matrix collects the various control sources and OR's the result
    // to activate relays, ToD overlays the result
    for (int out= 0;out<ctrlOuts;out++){
      bool result= ((ctrlMatrix[out][ctrlCtrl1]  || ctrlMatrix[out][ctrlCtrl2] ||
                     ctrlMatrix[out][ctrlCtrl3]  || ctrlMatrix[out][ctrlCtrl4] ||
                     ctrlMatrix[out][ctrlLogic]) && ctrlMatrix[out][ctrlToD])  ||
                     ctrlMatrix[out][ctrlExtReq] || ctrlMatrix[out][ctrlTLCmd];
      // handle ToD direct control
      if (!control.controlled(out+ioRelay1)
          && todCtrl.controlled(out+ioRelay1)
          && out+ioRelay1!=memory.getInt(datLogicOut))
        result= memory.getBool(statToDActive);
      // set output!
      memory.setBool(statRelay1Status+out,result);
      int state= LOW;
      if (result) state= HIGH;
      switch (out){
        case 0:
         digitalWrite(hdwrRelay1,state);
         break;         
        case 1:
         digitalWrite(hdwrRelay2,state);
         break;         
        case 2:
         digitalWrite(hdwrOutput1,state);
         break;         
        case 3:
         digitalWrite(hdwrOutput2,state);
         break;         
      }
    }
} //setOutputs

void checkStatus(){  
  uint16_t stat= 0;
  // startup
  if (memory.getBool(statStartup)) stat= stat | 1;
  // supply voltage
  if (memory.getFloat(datSupplyVoltage)<alarmVSupLow)  stat= stat | 2;
  if (memory.getFloat(datSupplyVoltage)>alarmVSupHigh) stat= stat | 4;
  // controller temperature
  if (memory.getUInt(datIntTempUnits)==unitsDegC
      && memory.getFloat(datIntTemp)>alarmIntTHigh) stat= stat | 8;
  if (memory.getUInt(datIntTempUnits)==unitsDegF
      && memory.getFloat(datIntTemp)>analogCtrl.CtoF(alarmIntTHigh)) stat= stat | 8;
  // WiFi
  if (!wifiStat) stat= stat | 16;
  // time
  if (!memory.getBool(statNTPTimeValid)) stat= stat | 32;
  // input channels valid, only if channel is in use
  if (control.controlled(ioWQAmp)   && !memory.getBool(statWQSensorValid)) stat= stat | 64;
  if (control.controlled(ioTemp1)   && !memory.getBool(statTemp1Valid))    stat= stat | 128;
  if (control.controlled(ioTemp2)   && !memory.getBool(statTemp2Valid))    stat= stat | 256;
  if (control.controlled(ioAnalog1) && !memory.getBool(statAnalog1Valid))  stat= stat | 512;
  if (control.controlled(ioAnalog2) && !memory.getBool(statAnalog2Valid))  stat= stat | 1024;
  // check control alarms
  if (memory.getBool(statCtrl1Alarm)) stat= stat | 2048;
  if (memory.getBool(statCtrl2Alarm)) stat= stat | 4096;
  if (memory.getBool(statCtrl3Alarm)) stat= stat | 8192;
  if (memory.getBool(statCtrl4Alarm)) stat= stat | 16384;
  if (memory.getBool(statCtrlAlarm))  stat= stat | 32768;
  // write results
  memory.setInt(datStatusCode,stat);
  if (memory.getBool(statStartup)) memory.setBool(statStatus,0);
  else memory.setBool(statStatus,stat==0); 
} // checkStatus

// handle encoder events
void encoderRight(ESPRotary& encodeRot){
  userCtrl.right();
}
void encoderLeft(ESPRotary& encodeRot){
  userCtrl.left();
}
void encoderClick(Button2& click){
  switch (click.getType()) {
    case single_click:
      userCtrl.click();
      break;
    case double_click:  
      userCtrl.dClick();
      break;
    case triple_click:
      userCtrl.dClick();
      break;  
    case long_click:
      userCtrl.press();
      break;
    }
} // encoderClick

// handle midnight reset and save parameter events
void checkMidnight(){
  if (timeCtrl.midnight()){  // wait for midnight
    if (memory.getBool(statMidnightSave)){
      Serial.print("Midnight save of EEPROM... ");
      memory.save();
    }
    if (memory.getBool(statMidnightReset)){
      Serial.print("Resetting processor... ");
      ESP.restart();
    }
  }
} // checkMidnight

void statLED(){
#ifdef hardwareS3Mini  // only the S3 has an RGB LED
  // send every quarter second
  if (millis()<pixelTime) pixelTime= 0;
  if (millis()-pixelTime<250) return;
  pixelTime= millis();
  if (memory.getBool(statStartup)) pixel.setPixelColor(0,180,255,0);
  else if (memory.getBool(statStatus)) pixel.setPixelColor(0,255,0,0);
  else{
    if (memory.getBool(statFlash)) pixel.setPixelColor(0,0,255,0);
    else pixel.setPixelColor(0,0,0,0);
  }
  // send it
  pixel.show();
#endif
  return;
} // statLED

//- Utility --------------------------------------------------------------------

// check for valid I/O channels
bool isIO(int chan){
  if (chan>=ioNone && chan<=ioTofD) return true;
  return false;
}
bool isDigital(int chan){
  if (chan==ioNone) return true;
  if (chan>=ioDigIn1 && chan<=ioFlash) return true;
  if (chan==ioTofD) return true;
  return false;
}
bool isOutput(int chan){
  if (chan==ioNone) return true;
  if (chan>=ioRelay1 && chan<=ioVState2) return true;
  return false;
}
bool isAnalog(int chan){
  if (chan==ioNone) return true;
  if (chan>=ioWQAmp && chan<=ioProcRead) return true;
  if (chan>=ioDays  && chan<=ioSeconds)  return true;
  return false;
}

// get the state of a digital channel
bool getChan(int chan){
  bool result= false;
  if (chan>=ioDigIn1 && chan<=ioFlash) result= memory.getBool(ioAddr[chan]);
  if (chan==ioTofD) result= memory.getBool(ioAddr[chan]);
  return result;
}

// get the value of an analog channel
float getAChan(int chan){
  float result= 0;
  if (chan>=ioWQAmp && chan<=ioProcRead) result= memory.getFloat(ioAddr[chan]);
  if (chan>=ioDays  && chan<=ioSeconds) result= memory.getInt(ioAddr[chan]);
  return result;
}

//- WiFI -----------------------------------------------------------------------
void wifiCheck(){
  if (wifiTime>millis()) wifiTime= 0; // handle millis rollover
  if (millis()-wifiTime>600000){ // check and retry every 10 minutes
    wifiTime= millis();
    if (!wifiStat) wifiConnect();
    if (wifiStat && !ModbusAvailable()) ModbusInit();       
  }
} // wifiCheck

void wifiConnect(){
  userCtrl.setScreen(scrWiFiStart);
  char ssid[18];
  char pass[18];
  char name[18];
  char hostName[28];
  char serNum[8];
  memory.getStr(datWifiAPName,ssid);
  memory.getStr(datWifiPassword,pass);
  memory.getStr(datControlName,name);
  Serial.println("  Initializing WiFi...");
  Serial.print("    SSID:");Serial.println(ssid);
  Serial.print("    Pass:");Serial.println(pass);
  strcpy(hostName,"SymbCtrl");
  for (int i=0;i<strlen(name);i++) if (!isAlphaNumeric(name[i])) name[i]= char(45);
  if (strlen(name)>1) {strcat(hostName,"-");strcat(hostName,name);} 
  else  {strcat(hostName,"-");ultoa(memory.getSerial(),serNum,10);strcat(hostName,serNum);}
  Serial.print("    Name:");Serial.println(hostName);
  WiFi.mode(WIFI_STA);
  WiFi.setHostname(hostName);  
  WiFi.begin(ssid,pass);
  unsigned long timeOut= millis();
  Serial.print("    Connecting ");
  while ((WiFi.status()!= WL_CONNECTED) && ((millis()-timeOut)<20000)){
    delay(500);
    Serial.print("-");
    userCtrl.service();
    }
  if (WiFi.status()==WL_CONNECTED){
    wifiStat= true;
    Serial.println("");
    Serial.println("    WiFi connected");
    Serial.print("    IP address: ");
    Serial.println(WiFi.localIP());
    wifiIPAddr= WiFi.localIP();
    timeCtrl.setTime(); 
    }
  else{
    wifiStat= false;
    Serial.println("");
    Serial.print("    WiFi connection failed to ");
    Serial.println(ssid);
    WiFi.disconnect(true);
    }
  wifiTime= millis();
  userCtrl.setScreen(scrWiFiDone);
} //wifiConnect
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
void loop() {
  wifiCheck();  
  if (wifiStat){
    ModbusService();
    ModbusHeartbeat();
  }
  timeCtrl.service();  
  userCtrl.service();  
  encodeRot.loop();
  encodeButton.loop();
  analogCtrl.readAll();
  procCtrl.service();
  control.service();
  logic.service();
  todCtrl.service();
  tlCtrl.service();
  countCtrl.service();
  memory.service();
  checkStatus();
  setOutputs();
  checkMidnight();
  statLED();
  // esp_task_wdt_reset();
} // loop

//- End Symbrosia Controller ---------------------------------------------------

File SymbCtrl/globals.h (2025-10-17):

/*------------------------------------------------------------------------------
  Globals - Symbrosia Controller
  Copyright © 2021 Symbrosia Inc.

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
--- revision record ------------------------------------------------------------

  26Dec2021 v0.1 A. Cooper
  - initial version
  16Apr2022 v1.0 A. Cooper
  - first release candidate
  16Dec2023 v2.0 A. Cooper
  - modify for Mark 2 PCB's
  20Mar2024 v2.4 A. Cooper
  - Added and tested support for Wemos ESP32-S2 Mini, S2 mini and S3 mini are
  the current processor module choices
  - removed support for ESP32 Saola and older rev PCB's
  - added monthly reset
  - added combined control alarms
  - added a few new units: ppm, day, hour, min, sec
  - added datFrequency to support frequency counter
  25Mar2024 v2.6 A. Cooper
  - added control enable source
  - added control one-shot flag
  - added TofD to IO channel list
  - added a few new units
  02Nov2024 v2.8 A. Cooper
  - move LCD screen constants here from userCtrl.h
  - add screen ID's for fixed data entry (92 to 94)
  - add screen ID's for firmware update (95)
  - add fixed data definitions (serial,hardware, processor)
  11Apr2025 v2.9 A. Cooper
  - remove unused timer and counter enable
  - added registers for time limited command, datTLCDuration 148,
  datTLCOutput 149, statTimeLimCmd 70, and statTimeLimFlag 71
  - expanded Modbus coil space to 80 registers

------------------------------------------------------------------------------*/
#pragma once

//#define hardwareS2Mini 2
//#define hardwareS3Mini 3
#define hardwareAuto 9

#ifdef hardwareAuto // attempt to ID processor from IDE
  #if defined(ARDUINO_LOLIN_S2_MINI)
    #define hardwareS2Mini 2
  #elif defined(ARDUINO_LOLIN_S3_MINI)
    #define hardwareS3Mini 3
  #else
    #error Undefined target processor!!
  #endif
#endif

#ifdef hardwareS2Mini
  #include "hardwareSymbCtrlS2Mini.h"
  #define modelNameStr  "SymbCtrl Mk2 S2"
  #define watchdogCores  1
#endif

#ifdef hardwareS3Mini
  #include "hardwareSymbCtrlS3Mini.h"
  #define modelNameStr  "SymbCtrl Mk2 S3"
  #define watchdogCores  2
#endif

// watchdog
#define watchdogTime   5 // watchdog timeout in seconds
// unit ID 
#define firmMajor      2
#define firmMinor      9
// default time zone
#define timeZone     -10
// alarm points
#define alarmVSupLow   8 // low supply voltage alarm point
#define alarmVSupHigh 16 // high supply voltage alarm point
#define alarmIntTHigh 55 // high internal temperature alarm point in C
// network loss time limits
#define timeNoNetMax   2 // time to indicate net loss in hours
#define timeNoNTPMax  48 // time to indicate NTP time invalid in hours
// startup lockout
#define startupDelay  30 // startup lockout in seconds\p\order\detail.html
// misc
#define forceSerial   false // force load of fixed data (serial, hardware, etc)
#define forceDefaults false // force load of defaults on boot

//- WiFi credentials -----------------------------------------------------------
#define defWiFi "SSID"
#define defPass "Pass"

//- ntp server -----------------------------------------------------------------
#define ntpServer1 "pool.ntp.org"
#define ntpServer2 "time.nist.gov"

// global variables and functions ----------------------------------------------
extern bool      wifiStat;
extern IPAddress wifiIPAddr;

// serial number
#define serialNumMin       100
#define serialNumStart     280
#define serialNumMax       999

// hardware ID codes...
#define hdwrIDmk1            1
#define hdwrIDmk2revA        2
#define hdwrIDmk2revB        3
#define hdwrIDmk2revC        4
#define hdwrIDmk2revD        5
#define hdwrIDmk2revE        6
#define hdwrIDMin            1
#define hdwrIDMax            4

// processor ID codes...
#define procIDS2Saola        1
#define procIDS2Mini         2
#define procIDS3Mini         3
#define procIDMin            1
#define procIDMax            3

// Output control...
#define ctrlOuts             4
#define ctrlRelay1           0
#define ctrlRelay2           1
#define ctrlOutput1          2
#define ctrlOutput2          3
#define ctrlSrcs             8
#define ctrlCtrl1            0
#define ctrlCtrl2            1
#define ctrlCtrl3            2
#define ctrlCtrl4            3
#define ctrlToD              4
#define ctrlLogic            5
#define ctrlExtReq           6
#define ctrlTLCmd            7

// I/O channels...
#define ioNone               0 // no I/O channel (no action)
#define ioWQAmp              1 // WQ sensor amplifier
#define ioTemp1              2 // temperature amplifier 1
#define ioTemp2              3 // temperature amplifier 2
#define ioAnalog1            4 // analog input 1
#define ioAnalog2            5 // analog input 2
#define ioIntTemp            6 // internal temperature
#define ioSupplyV            7 // supply voltage
#define ioProcRead           8 // processed reading
#define ioDigIn1             9 // digital input 1
#define ioDigIn2            10 // digital input 2
#define ioRelay1            11 // output relay 1
#define ioRelay2            12 // output relay 2
#define ioDigOut1           13 // digital output 1
#define ioDigOut2           14 // digital output 2
#define ioVState1           15 // virtual IO
#define ioVState2           16
#define ioCtrl1             17 // control outputs
#define ioCtrl2             18
#define ioCtrl3             19
#define ioCtrl4             20
#define ioCAlm              21 // Control loop alarms
#define ioC1Alm             22
#define ioC2Alm             23
#define ioC3Alm             24
#define ioC4Alm             25
#define ioC1AlmLo           26
#define ioC2AlmLo           27
#define ioC3AlmLo           28
#define ioC4AlmLo           29
#define ioC1AlmHi           30
#define ioC2AlmHi           31
#define ioC3AlmHi           32
#define ioC4AlmHi           33
#define ioFlash             34 // a flasher on/off 1Hz
#define ioDays              35 // day of month in decimal days 0.0 to 31.99d
#define ioHours             36 // time of day in decimal hours 0.0 to 23.99h
#define ioMinutes           37 // minutes and seconds in decimal 0.00 to 59.99m
#define ioSeconds           38 // seconds in decimal 0 to 59s
#define ioTofD              39 // time of day function result
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

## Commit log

2024-08-03 Add files via upload
    Add a couple photos of the controller
2024-08-03 Update README.md
    Add more material
2024-08-04 Delete src directory
    Rearrange to make downloading to the Arduino IDE possible
2024-08-04 Create README.md
    Rearrange to make integration with Arduino IDE possible
2024-08-05 Mods ro analogCtrl
    Added auto I2C address search to analogCtrl for MCP3021
2024-08-06 Add MBMon to repository
    [MBMon20240722.csv]
2024-08-25 Add Weather
    [MBMon20240722.csv, Weather20240824.csv, Weather20240825.csv]
2024-08-25 Ignore configuration files
    [Weather20240825.csv]
2024-09-27 Add STL files for PBR Controller
    [025-057 Subframe Lower.stl, 025-058 Control Knob.stl, 025-059 TBlock End.stl]
2024-09-27 Remove spaces from filenames
    [025-057SubframeLower.stl, 025-058ControlKnob.stl, 025-059TBlockEnd.stl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]
2024-10-26 Weather data
    [LabCtrl20240902.csv, LabCtrl20240903.csv, Weather20240826.csv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]
2024-11-01 Remove logfiles
    [MBMon20241101.csv, Weather20240826.csv, Weather20240827.csv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]
2024-11-01 Version 2.7 work
    [MBMon20241101.csv]
2024-11-02 Regression test v2.7
    [MBMon20241101.csv]
2024-11-02 Edit rev record
    [MBMon20241101.csv]
2024-11-02 Revert "Edit rev record"
    This reverts commit 24d97c7264457223542c1ffbeaa103c3e2f5fb02.
    [MBMon20241101.csv]
2024-11-16 Fixes to v2.8 prerelease
    [SymbCtrl.ino, globals.h]
2024-11-18 Bug hunt in v2.8
    [globals.h]
2024-11-19 Add PCB image
2025-04-15 Scrollable data frame
2025-04-16 Bind mouse wheel to scrolling
2025-04-26 SyCheck Work
    [Weather20240824.csv, Weather20240825.csv]
2025-06-03 Add PCB to repository
    [Controller BOM.xlsx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]
2025-06-04 PCB Rev C in work
    [Controller.kicad_pcb, Controller.kicad_sch]
2025-06-13 SymbCtrl 2.9 work
    [Controller.kicad_pcb, Controller.kicad_sch]
2025-07-10 Update to MBMon
    [Controller-B_Cu.gbr, Controller-B_Mask.gbr, Controller-B_Paste.gbr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]

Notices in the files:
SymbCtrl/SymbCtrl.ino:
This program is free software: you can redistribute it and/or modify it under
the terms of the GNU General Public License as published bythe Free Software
